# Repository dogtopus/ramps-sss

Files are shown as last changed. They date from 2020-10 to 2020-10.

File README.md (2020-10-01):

# RAMPS SSS

TMC2130 (SilentStepStick) SPI Adapter for RAMPS v1.4

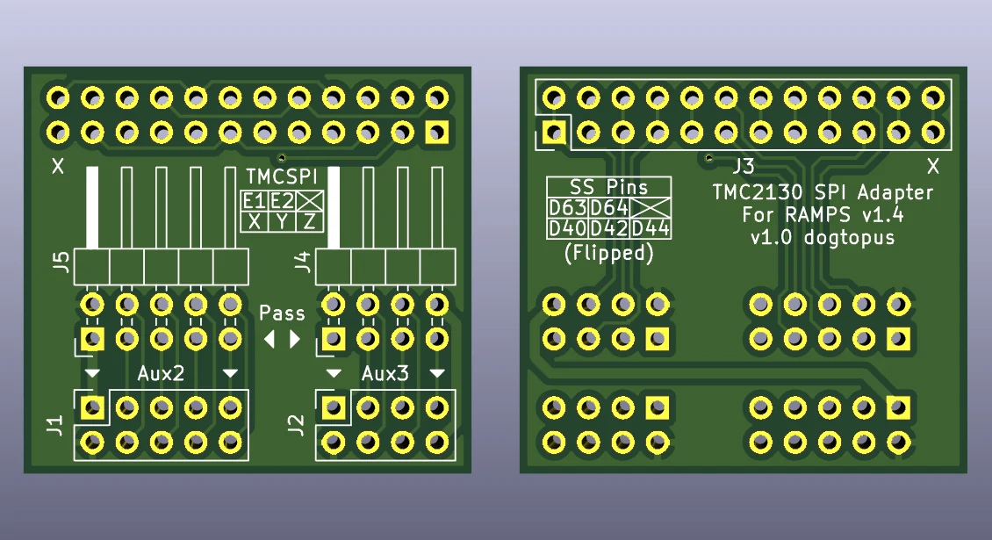
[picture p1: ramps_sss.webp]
ramps_sss


## Features

- Dedicated 4-pin connector for each TMC2130 unit. Works with either .1" cable assemblies or individual jumper wires.
- Intuitive pinouts.
- Passthrough connectors for both Aux2 and Aux3 enable access to unused pins. Can co-exist with SPI SD card reader.

## BOM

J1, J2: **Angled** double row female .1" header.
J3: Straight double row male .1" header (can also use 5x 4-position colored single row headers for better pin differentiation)
J4, J5: Angled double row male .1" header.

## SS pin allocations

| SS | Axis | RAMPS Pin | 
| --- | --- | --- |
| 0 | X | D40 |
| 1 | Y | D42 |
| 2 | Z | D44 |
| 3 | E0 | D63/A9 |
| 4 | E1 | D64/A10 |

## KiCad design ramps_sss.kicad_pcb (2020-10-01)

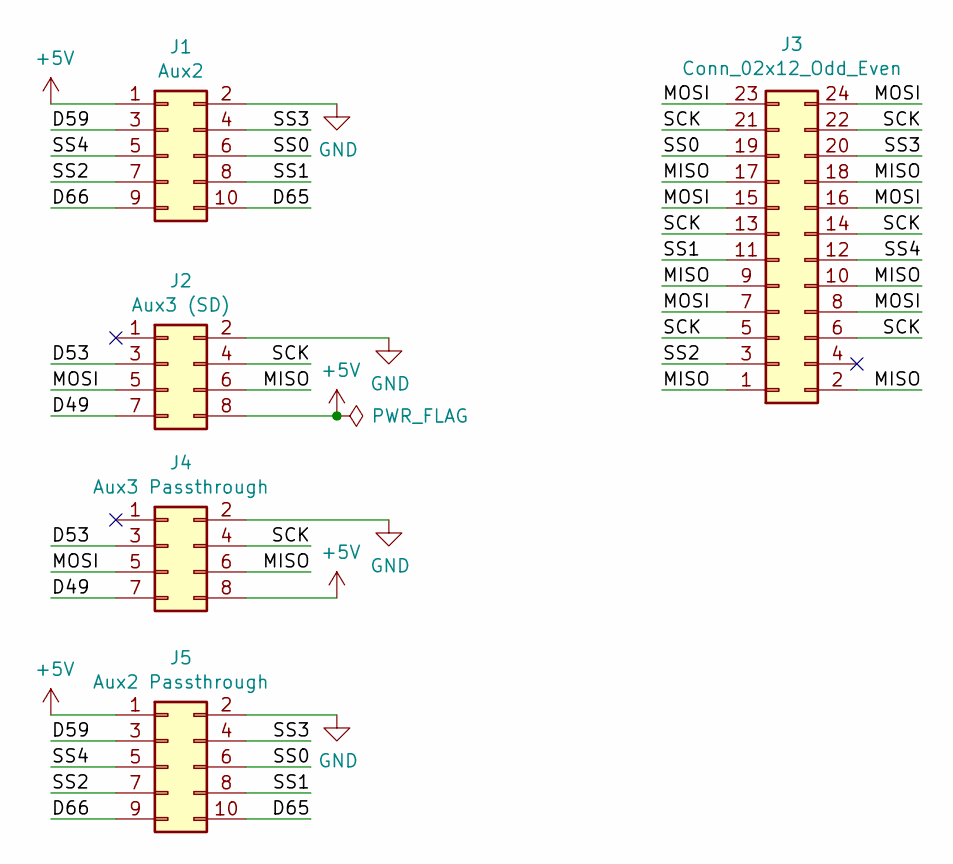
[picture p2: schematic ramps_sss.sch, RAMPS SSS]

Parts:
J1: Aux2; PinSocket_2x05_P2.54mm_Vertical
J2: Aux3 (SD); PinSocket_2x04_P2.54mm_Vertical
J3: Conn_02x12_Odd_Even; PinHeader_2x12_P2.54mm_Vertical
J4: Aux3 Passthrough; PinHeader_2x04_P2.54mm_Horizontal
J5: Aux2 Passthrough; PinHeader_2x05_P2.54mm_Horizontal

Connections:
+5V: J1.1, J2.8, J4.8, J5.1
/D49: J2.7, J4.7
/D53: J2.3, J4.3
/D59: J1.3, J5.3
/D65: J1.10, J5.10
/D66: J1.9, J5.9
/MISO: J2.6, J3.1, J3.2, J3.9, J3.10, J3.17, J3.18, J4.6
/MOSI: J2.5, J3.7, J3.8, J3.15, J3.16, J3.23, J3.24, J4.5
/SCK: J2.4, J3.5, J3.6, J3.13, J3.14, J3.21, J3.22, J4.4
/SS0: J1.6, J3.19, J5.6
/SS1: J1.8, J3.11, J5.8
/SS2: J1.7, J3.3, J5.7
/SS3: J1.4, J3.20, J5.4
/SS4: J1.5, J3.12, J5.5
GND: J1.2, J2.2, J4.2, J5.2

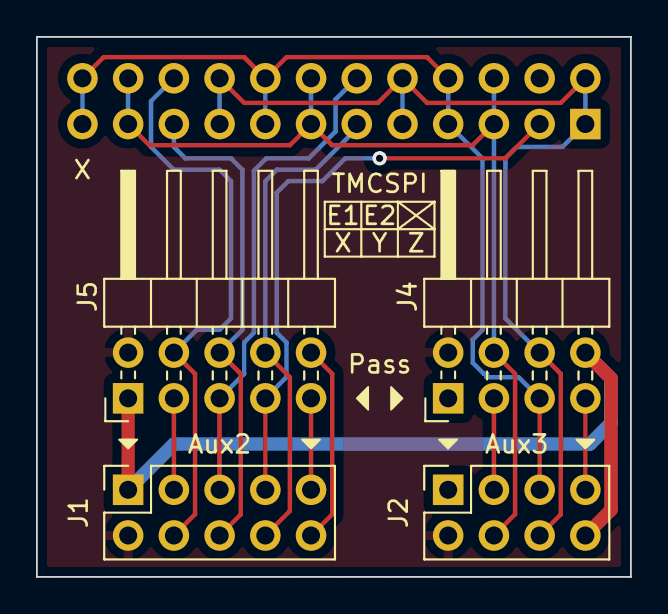
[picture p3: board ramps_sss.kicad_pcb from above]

Board: 2 copper layers, 33.0 x 30.0 mm, 5 parts (1 on the bottom side), 15 nets.
